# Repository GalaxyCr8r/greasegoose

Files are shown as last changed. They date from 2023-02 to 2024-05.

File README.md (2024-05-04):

# GreaseGoose BETA
A FlyCore-Based Full Auto Electric Foam Blaster

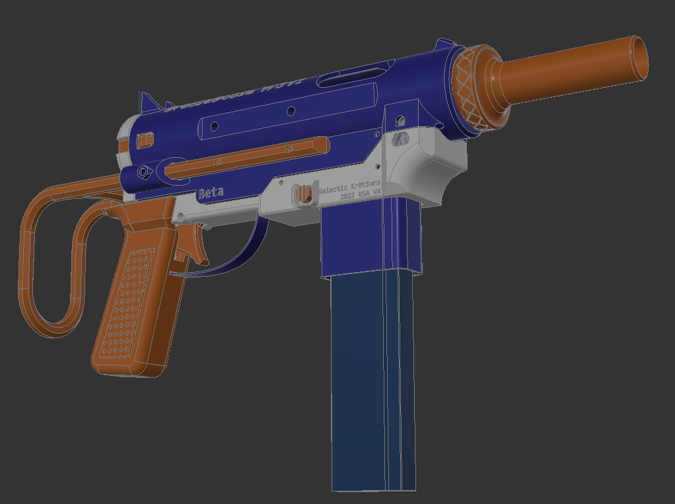
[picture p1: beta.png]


## Overview

As of 2/3/2023 these files are provided as-is with no warranty. Contact me before selling or distrubuting modified parts before release.

Work-in-progress manual can be found here: http://greasegoose.gkr8tions.com

Find me on Discord at GalaxyCr8r#6911 (You may need to join r/nerf, OFD, or FluxLab's discords to message me)

Uses the excellent FlyCore platform: https://github.com/oldfieldadamg/OFD_Flycore_Straight

### Options

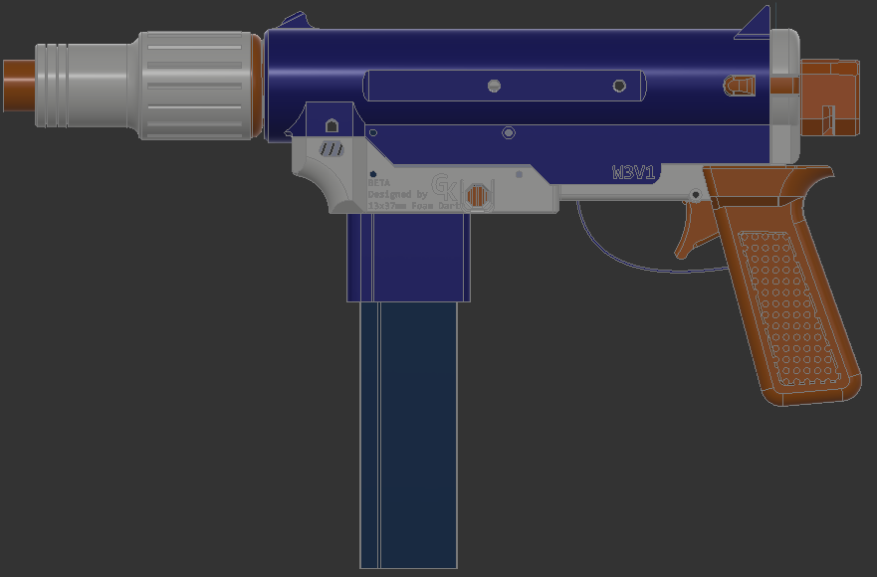
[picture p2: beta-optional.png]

Shown with the BCAR and N-Strike-compatible stock attachment point. Not shown: front and rear sling mounts.

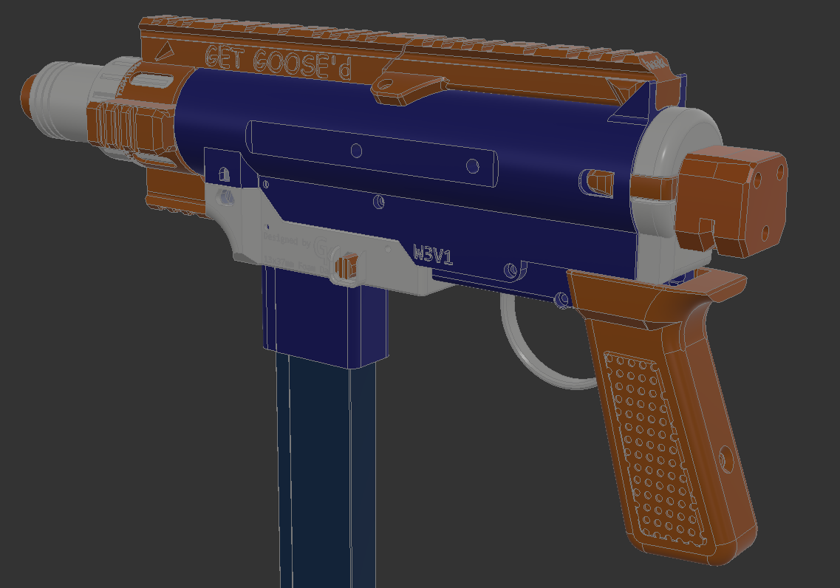
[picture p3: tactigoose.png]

Similar, but with the TactiGoose rail system.

## Bill of Materials

 - FTW- or Nightningale-compatible FlyCore
   - (2) 130 motors
   - (1) N20 Pusher Motor of your choice! (300- 3000rpm)
   - (4) m2x5mm motor screws
   - (8-9) M3 x 5mm diameter x 6mm deep heat set inserts (longer ones may not work)
   - (6) M2.6x12mm toy screws
   - (1) M2.6x10mm toy screw (Optional)
   - (1) Cherry DB2 style switch for pusher position (Optional)
   - (1) Spring 20mm in length less than 7mm in diameter for mag release (Recommend McMaster 9657K297 Trimmed to ~20-22mm)
 - (1) Dart Head
 - (1) 21A Microswitch (Genuine Omron) Lever-Style (https://outofdarts.com/products/21a-microswitch-genuine-omron-v-212-1c6-spdt)
 - (1) 10A Microswitch (Cherry DB2 pin plunger) Plunger-Style (https://outofdarts.com/products/10a-microswitch-cherry-db2-plunger)
 - (2) M2.6x12mm toy screws (One can be longer than the other)
 - (1) M3x25mm
 - (2) M3x16mm
 - (6) M3x10mm
 - (2-4) M3x8mm
 - (2-3) M3x6mm
 - (3-5) M3 Threaded Heat-Set Inserts
 - Optional Parts:
   - BCAR Muzzle:
      - (9) 3x7x3 F683ZZ flanged bearings
      - (9) 3x14mm pins
      - Available Amazon, Alibaba, and Moose Mod Shop: https://moose-mod-shop.myshopify.com/products/3-3x7x3-bcar-bearings-and-pins
   - Fidlock:
      - M4 heat-set threaded inserts
      - Fidlock magnets (https://outofdarts.com/products/fidlock-snap-male-bolt-magnet-medium)
   - Split Receiver: M3x6mm screw
   - NStrike Stock:
      - (3) M3 Threaded Heat-Set Insert OR 3x M3 Hex Nuts
      - (3) M3x18mm

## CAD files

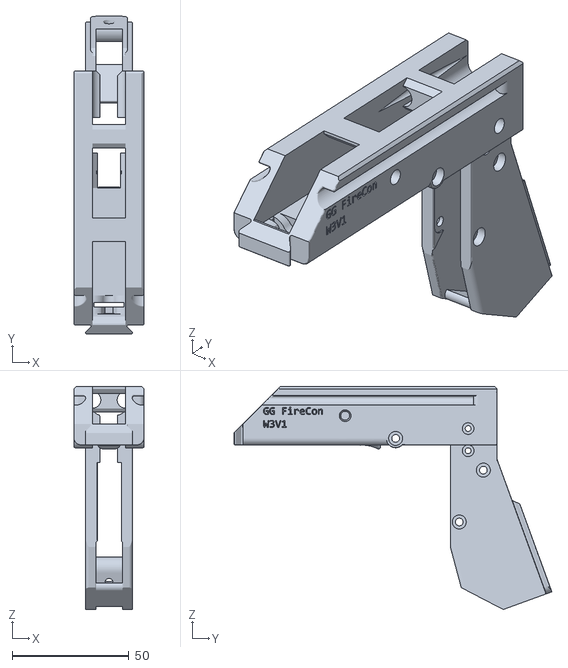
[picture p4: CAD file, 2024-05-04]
grip/FireControl.stl
30.0 x 136.0 x 95.4

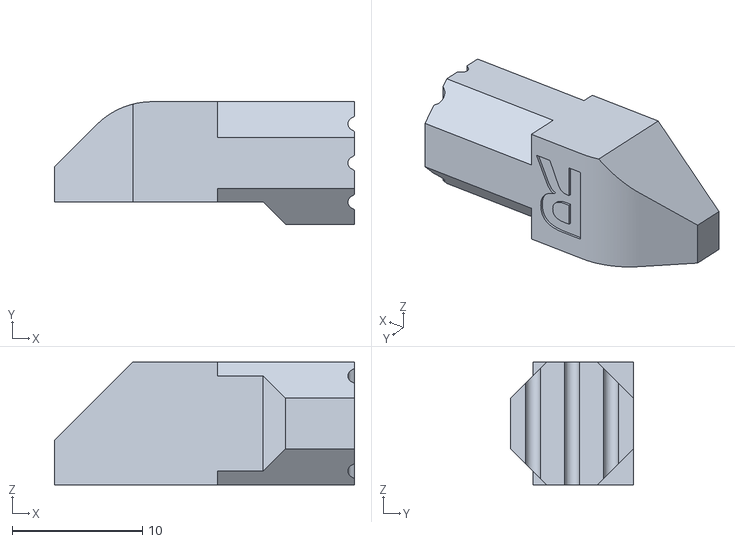
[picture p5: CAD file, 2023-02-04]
lower/MagButton_Right.stl
23.0 x 9.40 x 9.40

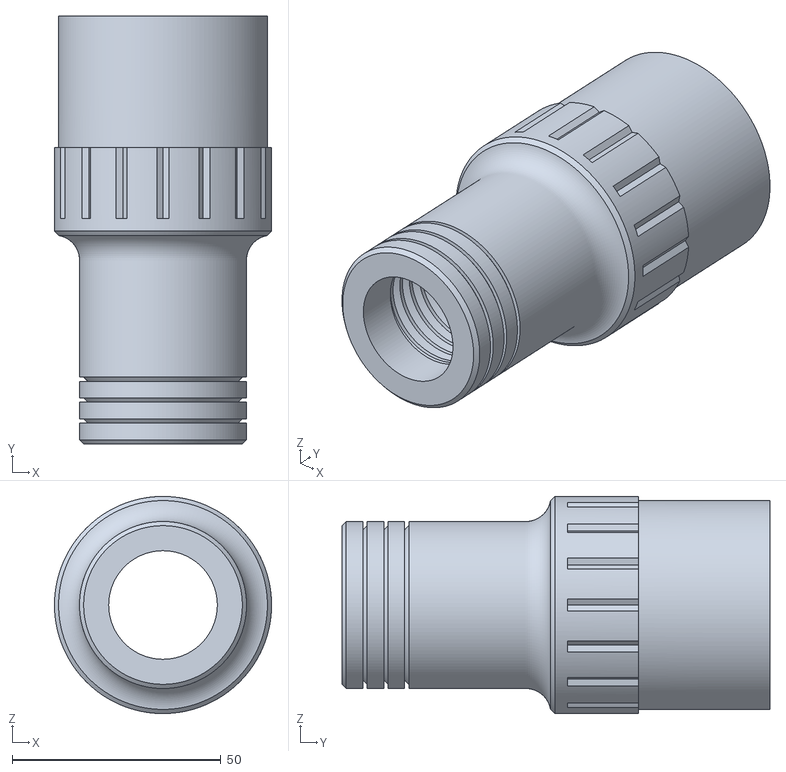
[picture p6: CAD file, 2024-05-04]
upper/Muzzle_BCAR_Shroud_forTactiGoose.stl
52.0 x 102.5 x 52.0

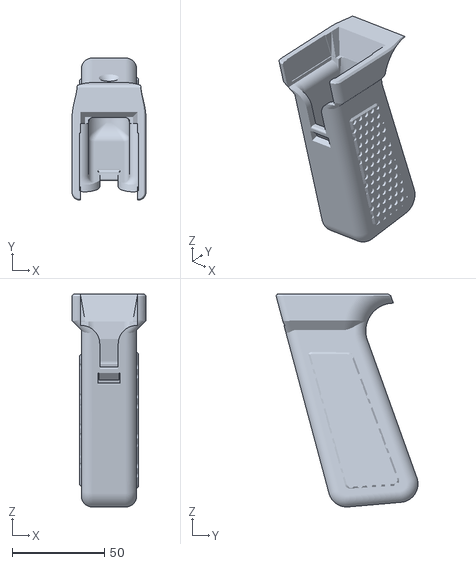
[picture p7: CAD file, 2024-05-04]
grip/Grip.stl
40.0 x 76.8 x 115.2

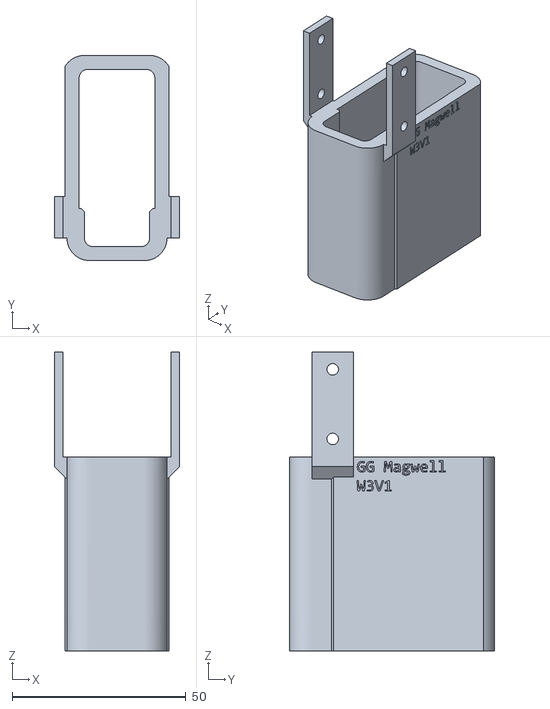
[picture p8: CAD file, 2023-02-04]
lower/MagWell.stl
36.0 x 59.0 x 86.0

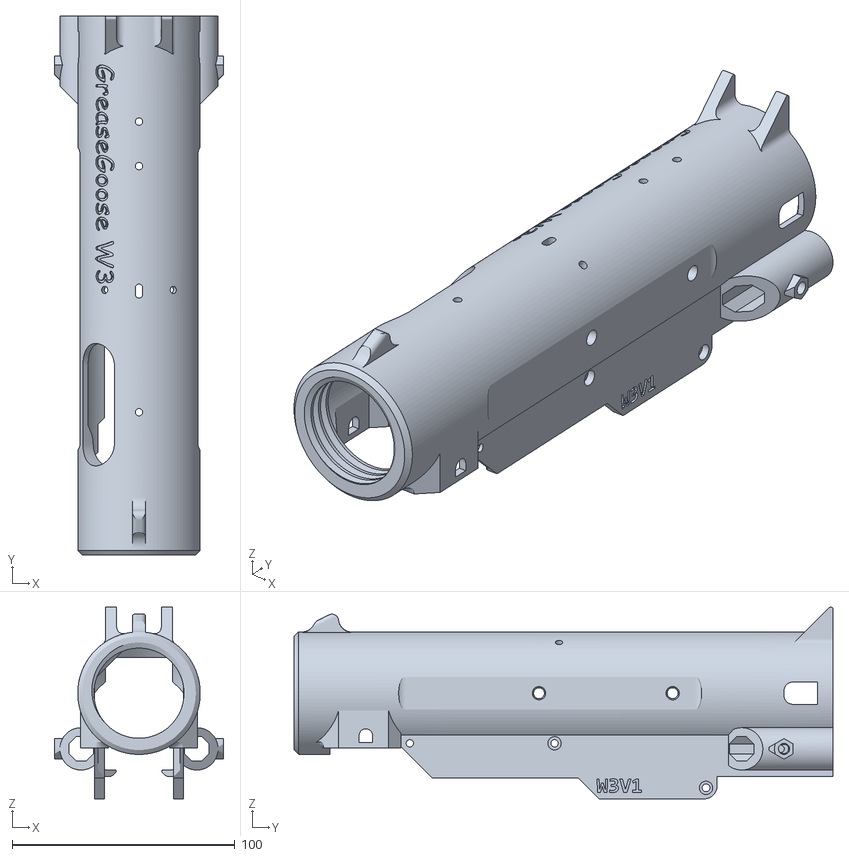
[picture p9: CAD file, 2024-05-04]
upper/UpperReceiver.stl
76.0 x 242.0 x 86.2

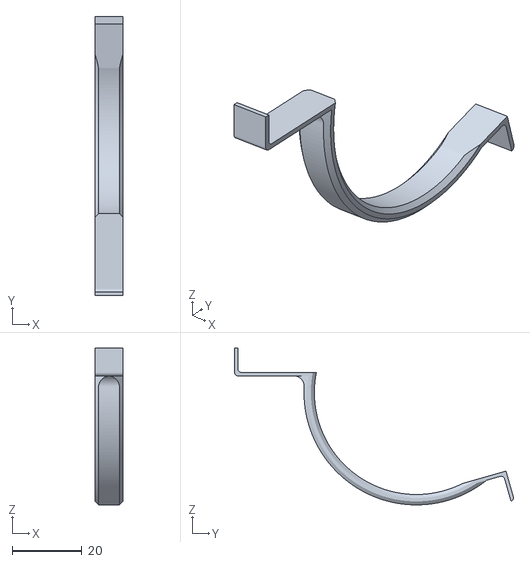
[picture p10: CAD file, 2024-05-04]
grip/TriggerGuard-v2.stl
8.00 x 80.2 x 45.1

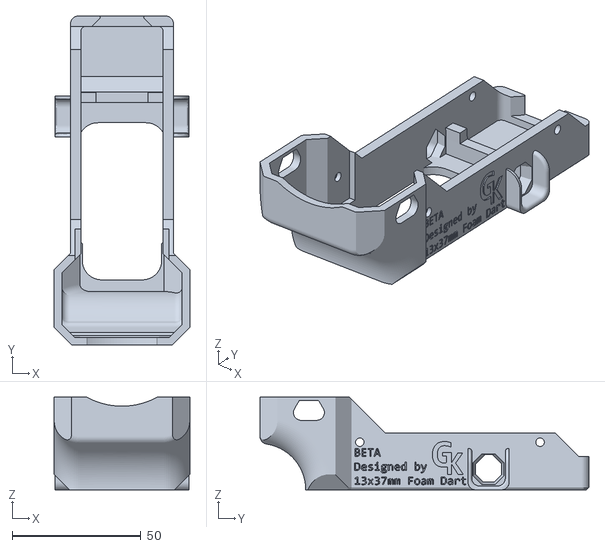
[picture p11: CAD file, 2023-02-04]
lower/LowerReceiver.stl
52.7 x 127.8 x 36.0

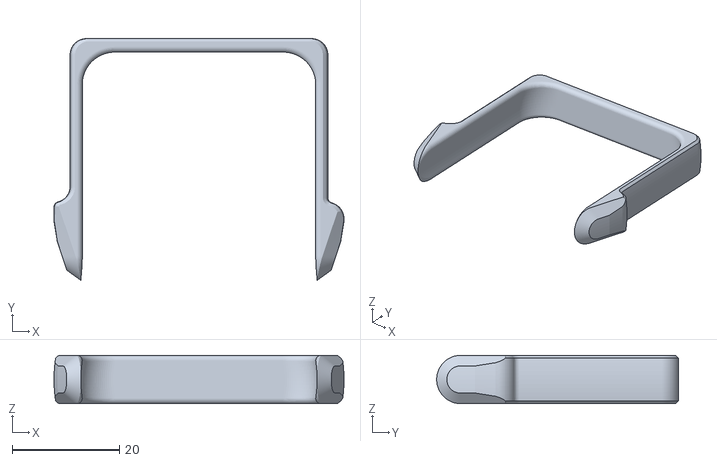
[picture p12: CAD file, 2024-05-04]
upper/RearDoorStrap_plus9mm.stl
54.0 x 45.0 x 9.00

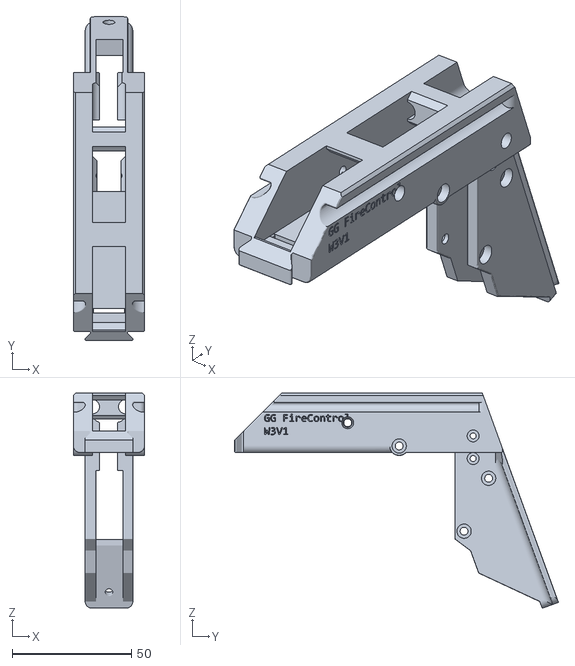
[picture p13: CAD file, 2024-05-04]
grip/FireControl_forSplitUpper.stl
30.0 x 136.0 x 90.2

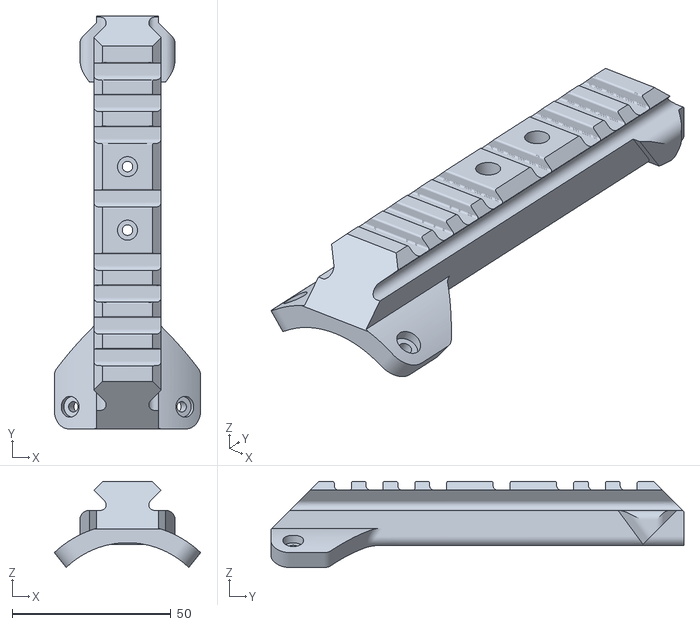
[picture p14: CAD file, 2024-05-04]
upper/RearRail.stl
46.1 x 130.0 x 27.1

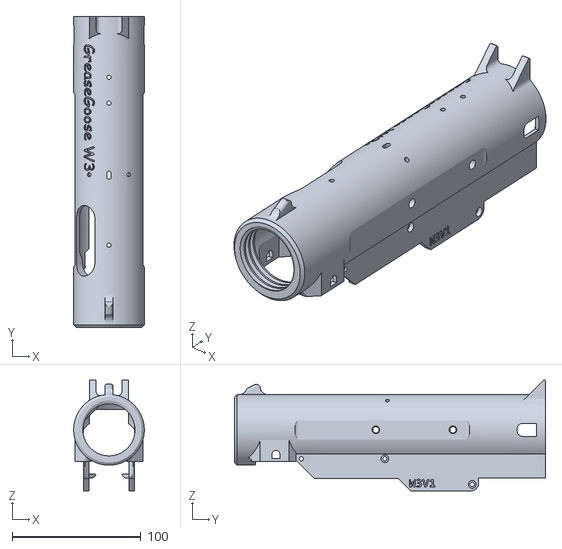
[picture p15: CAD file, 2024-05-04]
upper/UpperReceiver_withoutWireStock.stl
55.0 x 242.0 x 86.2

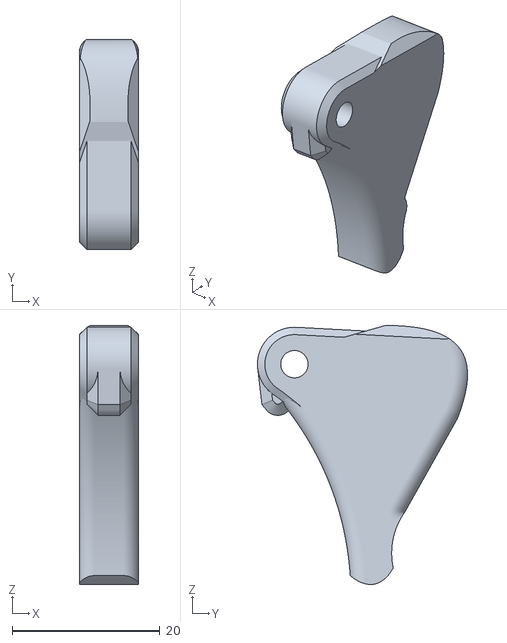
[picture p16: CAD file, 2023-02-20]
grip/Trigger.stl
8.00 x 28.4 x 35.1

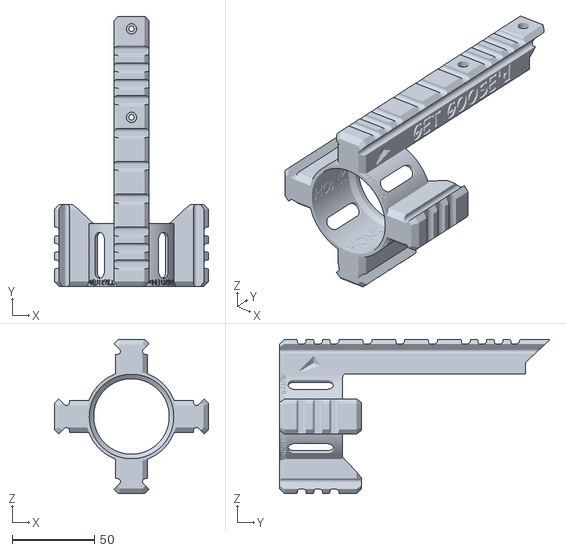
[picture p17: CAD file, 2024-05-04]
upper/TactiGoose_Front.stl
94.0 x 164.5 x 94.0

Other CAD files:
lower/MagButton_Left.stl
upper/SplitUpper_Forward_TactiGoose.stl
upper/SplitUpper_Rear_TactiGoose.stl
upper/SplitUpper_Rear_TactiGoose_withoutWireStock.stl
grip/TriggerGuard.stl
upper/ForwardSlingPoint.stl
upper/Muzzle.stl
upper/Muzzle_19mmOD.stl
upper/Muzzle_BCAR.stl
upper/Muzzle_BCAR_Shroud.stl
upper/Muzzle_MediumLength.stl
upper/RearDoor.stl
upper/RearDoorStrap.stl
upper/RearDoorStrap_0.5mmTighter.stl
upper/RearDoorStrap_1.0mmTighter.stl
upper/RearDoorStrap_1.5mmTighter.stl
upper/RearSlingPoint.stl
upper/SplitUpper_Forward.stl
upper/SplitUpper_Rear.stl
upper/SplitUpper_Rear_withoutWireStock.stl
upper/Stock-Short.stl
upper/Stock.stl
upper/StockAttachPoint.stl
upper/TactiGoose_RearRail.stl

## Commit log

2023-02-04 Beta Release 0.1
    [FireControl.stl, ForwardSlingPoint.stl, Grip.stl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]
2023-02-05 Added threaded insert to split upper
    Also added details to shroud
    [Muzzle_BCAR_Shroud.stl, SplitUpper_Forward.stl, SplitUpper_Rear.stl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]
2023-02-06 Rough BoM
2023-02-14 New two-part rear door
    [RearDoor.stl, RearDoorStrap.stl]
2023-02-20 8 File changes, number 2 will SHOCK you!!
    Corrected the new threaded insert holes and file location of the FireControl_forSplitUpper, bulked up the trigger stop so hopefully it won't fling itself forward so much. RearDoorStraps now state how much tigher they are, also added 1.5mm and added a version of the one piece upper that doesn't have the wire stock rings.
    [FireControl_forSplitUpper.stl, RearDoorStrap_0.5mmTighter.stl, RearDoorStrap_1.0mmTighter.stl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]
2023-02-20 Updated landing page.
2023-03-08 Tweaks
    Made the trigger guard slightly thicker and should actually be able to be put in place now. One end requires a nut and a M3 screw.
    Added a medium muzzle for those who want short but don't want the tight inner diameter of the 19mmOD Muzzle.
    Changed the screw hole for the split upper rear to use the same method as the other screw holes.
    [FireControl.stl, Grip.stl, Muzzle_19mmOD.stl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]
2023-03-16 Short Stock + Noidcore support
    Cut out a slot for the noidcore in UpperRcv and SplitUpper_Fwd.
    Added labels to both sides of the split rcv.
    Added a Short version of the stock that should print on a 180x180 print bed.
    [SplitUpper_Forward.stl, SplitUpper_Rear.stl, SplitUpper_Rear_withoutWireStock.stl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]
2023-03-28 Removed bespoke FireCon for split upper
    Now ALL upper receivers have holes to screw into the fire control part for added stability.
    Also, the Fire Control now allows you to slide the big switch in from the back. This should aid in assembly if you wire the switches after the fly core.
    [FireControl.stl, FireControl_forSplitUpper.stl, UpperReceiver.stl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]
2023-04-30 Create FireControl_forSplitUpper.stl
    Updated FireControl_forSplitUpper to now be printed on the back instead of on the top. This will provide much better strength
    [FireControl_forSplitUpper.stl]
2024-05-04 TACTIGOOSE!
    Lots of improvements from Beta feedback
    - New TactiGoose rail system.
    - Improved wire channels in the fire control.
    - Improved wire area for Grip
    - Completely redone TriggerGuard
    [FireControl.stl, FireControl_forSplitUpper.stl, Grip.stl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]
2024-05-04 Create Muzzle_BCAR_Shroud_forTactiGoose.stl
    Because the original BCAR doesn't have good clearance inside TactiGoose front.
    [Muzzle_BCAR_Shroud_forTactiGoose.stl]
